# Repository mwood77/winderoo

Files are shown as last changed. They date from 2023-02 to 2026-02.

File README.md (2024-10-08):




<div align="center">  
  <h2>
    Winderoo
    <p><i>Open source firmware for microcontolled watch winders</i></p>
  </h2>
</div>

<div align="center"> 
  <a href="https://www.youtube.com/watch?v=BJKpY6Zp8BI" target="_blank">
    Winderoo - The Open Source Watch Winder
  </a>
  <br>
  <br>
  <p>
    Winderoo is open source firmware which adds <i>smart functionality</i> to your <a href="https://github.com/mwood77/osww" target="_blank">OSWW build</a> or microcontroller equipped watch winder. <i>Smart functionality</i> includes a Web UI (fully-translated in 5 languages!), OLED screen support, start timer, and more!
  </p>
</div>

> [!NOTE]
> OSWW is an open source modular watch winder, which you can read more about on [GitHub](https://github.com/mwood77/osww) or [Printables](https://www.printables.com/model/421249-osww-the-open-source-watch-winder).

### Key Features
* Settable RPD (rotations per day) between 100 - 960rpd
* Single direction (clockwise / anti-clockwise) or bi-directional winding.
* Settable start time. Have it wind while you're asleep, or while you're away, or anytime for that matter. 
* Manual cycle start / stop.
* 3 seconds of rest after 3 minutes of rotation, in every mode.
* Estimated cycle duration (how long it'll take to wind your watch).
* Cycle progress display (how far along the current winding routine is).
* Software or optional physical button to trigger ON/OFF state, so you can disable the winder completely.
* OLED screen support
* Simple setup. Flash the firmware and File System with a few clicks, then connect your phone (or other device) to the winder's setup wifi network & add it to your home network.
* There's no app required! You control it from a web browser.
* Minimal electronics / programming experience required
* Web UI is fully translated into 5 languages (more are welcome!)

### Winderoo Requires a Different Microcontroller
* **You must replace the Pi Pico, as spec'd in the OSWW build guide, with an ESP32. This project will not run on a Pi Pico!**

# User Manual
* [Click Here to see the user manual](./docs/user-manual.md)

## Prerequisites
> [!IMPORTANT]
> This project is an add-on to your already built [Open Source Watch Winder (OSWW)](https://github.com/mwood77/osww)

#### Download and install the following on your computer:
1. [Visual Studio Code](https://code.visualstudio.com/)
1. [PlatformIO](https://platformio.org/install/ide?install=vscode)
    - Note: the "extensions" button has changed since Platformio has created their install guide. You can access the extensions pane with the following key combinations:
        - Windows: Ctrl+Shift+X
        - macOS: Command+Shift+X
1. You may or may not need these drivers, but some 'knock off' ESP32 dev boards require them.
    - [CP210x Drivers](https://www.silabs.com/developers/usb-to-uart-bridge-vcp-drivers?tab=downloads) 
    - If the CP210x drivers don't work:  [CH340 Drivers](https://learn.sparkfun.com/tutorials/how-to-install-ch340-drivers) 

## Build Instructions
1. [Bill of Materials (what you need to buy)](./docs/bom-requirements.md)
1. [Software Installation](./docs/install-software.md)
1. [Winderoo Wiring Diagram](./docs/wiring-diagram.md)

## Contributing
This project welcomes contributions. Please follow the regular git workflow; fork + PR to contribute.

### Translations / Localization
Winderoo has multi-language support, and we welcome adding more languages.

To add another language:
1. Duplicate one of the current localizations, and translate the text:
    - `src/angular/osww-frontend/src/assets/i18n/` stores the current localizations.
1. Add a new language menu item here to enable your language:
    - `src/angular/osww-frontend/src/app/header/header.component.html`
1. Open a Pull Request

### Frontend
- Angular with Angular Material
- [Frontend Readme](./src/angular/osww-frontend/README.md)

### Backend 
- C++ based API with mDns, a web server, local file system, and a bunch of other things.

### API Specification

The API has 4 endpoints. You can explore them in the attached Open API definition.
- [Open API Definition](./openapi.yml)

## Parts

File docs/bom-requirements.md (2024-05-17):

> [👈 Back to main page](../README.md)

# Bill of Materials & Cost

> [!IMPORTANT]
> This project is an add-on to your already built [Open Source Watch Winder (OSWW)](https://github.com/mwood77/osww). 

- This microcontroller replaces the Pi Pico used in the OSWW.
- The Raspberry Pi Pico is incompatible with this project and must be swapped out.

### Total cost of required Parts
- **$8.00 (April 2023)**

> [!NOTE]
> The following tables contains affiliate links to Aliexpress; you do not pay an inflated price because of this. Should you decide to use another supplier, please ensure that you cross-reference this table and buy identical components.
>
> While most of these components are standardized, I will not be able to assist you if you purchase your components from a separate supplier, as the winder was designed around the components (as supplied) beneath.

| |  Quantity per Order | Link / Part Name |  Comments |  Cost Incl. Shipping |
| :-: | :---: | :---: | :---: |:-----:|
| 🔲 | 1 | [ESP32 Dev Kit](https://s.click.aliexpress.com/e/_Derbd5r) | Select `Color: ESP32` | $8.00 |

### Optional parts
The following parts list will allow you to add:
- 1x SSD1306 compatible OLED screen (0.96" size)
- 1x MX1508 Motor Controller. This is a much smaller DC motor controller. Winderoo supports granular motor control with this board (PWM control); you must set a build flag to use this, which has a callout step during the [software installation instructions](./install-software.md).

| |  Quantity per Order | Link / Part Name |  Comments |  Cost Incl. Shipping |
| :-: | :---: | :---: | :---: |:-----:
| 🔲  | 1 | [0.96" SSD1306 OLED](https://s.click.aliexpress.com/e/_DFywAW1) | Select: whichever colour you'd like! | $2.00 |
| 🔲  | 1 | [MX1508 Miniature Motor Controller (PWM)](https://www.aliexpress.com/item/4000408025093.html) |  | $3.00 |

## Next Steps
> [Proceed to software installation 👉](./install-software.md)

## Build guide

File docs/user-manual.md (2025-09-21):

> [👈 Back to main page](../README.md)

# User Manual

#### Contents
- [Winderoo's Web User Interface](#winderoos-web-user-interface)
- [Winderoo's Home Assistant Interface](#winderoos-home-assistant-interface)
- [Winderoo's LED Blink Status](#winderoos-led-blink-status)

## Winderoo's Web User Interface

| v1.1.0 | |
| :---: |:---: |
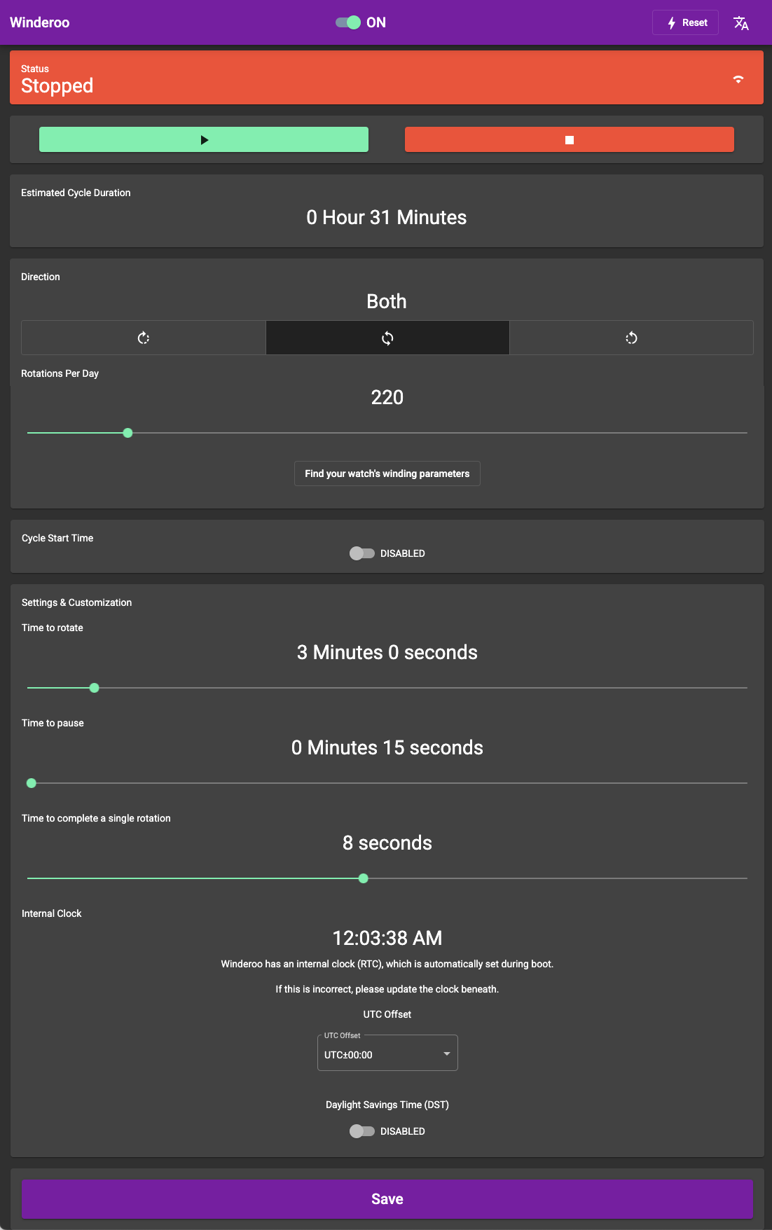
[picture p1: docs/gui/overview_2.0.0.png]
|  | This is winderoo's primary interface. From here you can change any settings you need |

### Enable / Disable Winding
| UI Element | Function |
| :---: |:---: |
|  | This is a software switch, which will _completely enable or disable_ the winder's ability to wind. When the switch is set to **OFF**, Winderoo will not wind or begin winding at a your desired 'Cycle Start Time.' If you choose to attach an (optional) physical button, the code will automatically toggle this switch when you press the button. |

### Reset / Change WiFi Network
| UI Element | Function |
| :---: |:---: |
|  | This is will open a pop-up window, which will ask you to confirm reset, and walk you through the reset procedure. Use this to change the WiFi network Winderoo connects to. |
|  | This will open a pop-up menu where you can select which language you'd prefer. |

### Status Bar
| UI Element | Function |
| :---: |:---: |
|  | Winder is not winding |
|  | Winder is winding |
| | Wifi Status - this behaves as you'd expect |

### Control Buttons
| UI Element | Function |
| :---: |:---: |
|  | _begin_ winding immediately, using saved settings |
|  | _stop_ winding immediately |

### Progress Indicator
> The progress indicator only appears while actively winding

| UI Element | Function |
| :---: |:---: |
|  | While animated, Winderoo is attempting to update the progress indicator |
|  | The progress of the current winding routine |

### Estimated Cycle Duration
| UI Element | Function |
| :---: |:---: |
|  | An estimation of how long the your current winding routine will take, start to finish |

### Winder Control
| UI Element | Function |
| :---: |:---: |
|  | Which direction Winderoo should turn. The available options are 'Clockwise,' 'Both' (clockwise + counter-clockwise), and 'Counter-Clockwise' |
|  | How many full rotations Winderoo should complete per routine |
|  | Launches a new browser tab to an external, 3rd party website. This resource hosts winding parameters for most major watch manufacturers |

### Cycle Start Time
| UI Element | Function |
| :---: |:---: |
|  | This will enable or disable the winder's timer. When the switch is set to **ENABLED**, Winderoo will begin winding at a your desired 'Cycle Start Time.' If the switch is set to **DISABLED**, you must start the winder using the [control buttons](#control-buttons) |
|  | Set which time you'd like Winderoo to begin winding at. **_Important!_** Winderoo will _always_ start at this time, even if you've already triggered a manual run with a [control button](#control-buttons). To stop this behavior, see: [Enable / Disable Winding](#enable--disable-winding) |

### OLED Screen

>[!IMPORTANT]
> This element will appear _only if_ you've compiled Winderoo with an OLED screen attached, and set the build flag accordingly.

| UI Element | Function |
| :---: |:---: |
|  | This will toggle the attached OLED screen on and off. |

### Screen Scheduling

> This functionality is only available when OLED screen is enabled.

| UI Element | Function |
| :---: |:---: |
|  | Enable or disable automatic screen scheduling. When enabled, the screen will automatically turn on and off based on the configured time schedule. |
|  | Set the time when the screen should turn on (24-hour format). |
|  | Set the time when the screen should turn off (24-hour format). |

**Note:** Screen scheduling works independently of manual screen control. When scheduling is enabled, the screen will automatically turn on/off based on the schedule, but you can still manually control the screen through the OLED toggle or Home Assistant integration.

### Settings & Customization

| UI Element | Function |
| :---: |:---: |
| | This sets the amount of time to rotate between pauses. Default is `3 minutes` |
| | This sets the amount of time to pause between rotation cycles. Default is `15 seconds` |
|  | This sets the amount of time it takes the winder to complete one full rotation. This value should only be changed if you've used a different motor, different gearing, or have retrofitted Winderoo into a off-the-shelf winder |
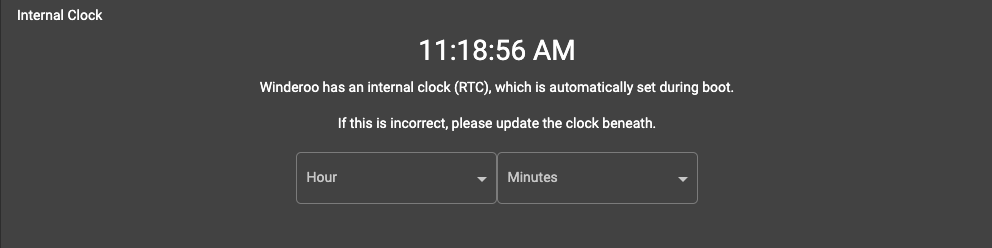
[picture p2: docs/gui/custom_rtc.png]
| | This reflects Winderoo's real time clock (RTC). This is set automatically using an NTP Pool. By default Winderoo's UTC offset is set to `0`. For accurate timekeeping, you must set this offset to your current location. You can use a site like [timeanddate.com](https://www.timeanddate.com/time/zone/timezone/utc) to search for your city and find your UTC offset. |

### Save / Update Settings
| UI Element | Function |
| :---: |:---: |
|  | This will capture and save all settings (including customizations). If a winding routine is currently running, it does not reset the current routine (it will update and finish accordingly). If you wish to make sure the routine is changed, manually stop, then start the routine. See [control buttons](#control-buttons). |

## Winderoo's Home Assistant Interface

>[!IMPORTANT]
> Home Assistant entities will only appear you've compiled Winderoo with the `HOME_ASSISTANT_ENABLED` build flag set to `TRUE`. If you're unsure how to do this, see the "**Build Options**" step under "*Flashing your microcontroller*" heading on the [Install Software](./install-software.md) documentation page.

If you've enabled Winderoo's Home Assistant integration, Winderoo will stream a number of entities into Home Assistant over MQTT. If you're unsure what MQTT or need to set this up in Home Assistant, [please see this document](https://www.home-assistant.io/integrations/mqtt).

Winderoo should be automatically discovered by Home Assistant within 60 seconds. The following entities are available to Home Assistant:
```yml
 -  button.winderoo_start
 -  button.winderoo_stop

 -  sensor.winderoo_status                                    : "Winding | Stopped"
 -  sensor.winderoo_wifi_reception                            : "Excellent | Good | Fair | Poor"
 -  sensor.winderoo_rtc_epoch_time                            : <unix epoch>
 
 -  number.winderoo_rotations_per_day                         : 100 <-> 960 
 -  number.winderoo_time_to_rotate                            : 100 <-> 960 
 -  number.winderoo_time_to_pause                             : 10 <-> 900 
 -  number.winderoo_duration_to_complete_a_single_rotation    : 1 <-> 16 

 -  select.winderoo_direction                                 : "CCW | BOTH | CW"
 -  select.winderoo_hour                                      : 00 <-> 23
 -  select.winderoo_minutes                                   : 00 <-> 50
 -  select.winderoo_rtc_hour                                  : 00 <-> 23
 -  select.winderoo_rtc_minutes                               : 00 <-> 59
 
 -  switch.winderoo_timer_enabled                             : "true | false"
 -  switch.winderoo_oled                                      : "true | false"
 -  switch.winderoo_power                                     : "true | false"
 -  switch.winderoo_screen_schedule_enabled                   : "true | false"
 -  select.winderoo_screen_schedule_start_hour                : 00 <-> 23
 -  select.winderoo_screen_schedule_start_minute              : 00 <-> 50
 -  select.winderoo_screen_schedule_end_hour                  : 00 <-> 23
 -  select.winderoo_screen_schedule_end_minute                : 00 <-> 50
```

You can replicate Winderoo's GUI with a basic Home Assistant card:
<table align="center">
  <tr>
    <th>Home Assistant GUI</th>
    <th>Code</th>
  </tr>
  <tr>
    <td>
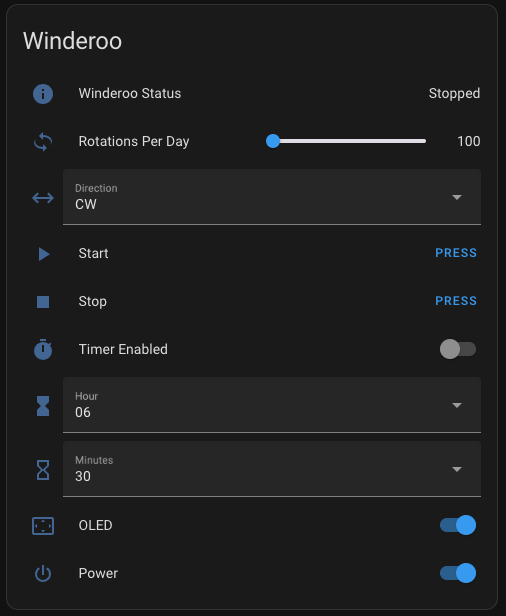
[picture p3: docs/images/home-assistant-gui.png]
        
    </td>
    <td>
<pre><code>
type: entities
entities:
- entity: sensor.winderoo_status
- entity: number.winderoo_rotations_per_day
    name: Rotations Per Day
- entity: select.winderoo_direction
    name: Direction
- entity: button.winderoo_start
    name: Start
- entity: button.winderoo_stop
    name: Stop
- entity: switch.winderoo_timer_enabled
    name: Timer Enabled
- entity: select.winderoo_hour
    name: Hour
- entity: select.winderoo_minutes
    name: Minutes
- entity: switch.winderoo_oled
    name: OLED
- entity: switch.winderoo_power
    name: Power
title: Winderoo
show_header_toggle: false
</pre></code>
    </td>
  </tr>
  <tr>
    <td>
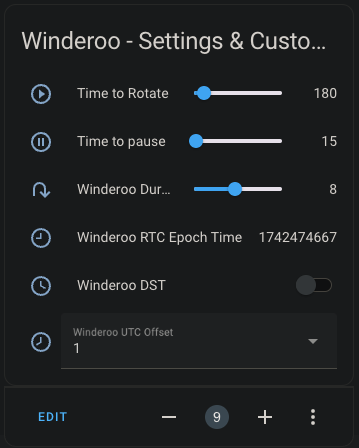
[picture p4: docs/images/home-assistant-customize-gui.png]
        
    </td>
    <td>
<pre><code>
type: entities
entities:
  - entity: number.winderoo_time_to_rotate
    name: Time to Rotate
  - entity: number.winderoo_time_to_pause
    name: Time to pause
  - entity: number.winderoo_duration_to_complete_a_single_rotation
  - entity: sensor.winderoo_rtc_epoch_time
  - entity: switch.winderoo_dst
  - entity: select.winderoo_utc_offset
title: Winderoo - Settings & Customization
</pre></code>
    </td>
  </tr>
</table>

## Winderoo's LED Blink Status

- Most ESP32 dev boards have a primary RED LED that is always on. This cannot be shut off via firmware. 
    - If you find it bothersome, you can cover it with electrical tape, de-solder it, or cut the trace with an x-acto knife.

- Most ESP32 dev boards have a secondary BLUE LED, however some may be a different colour. 
    - Please use the following table to understand what Winderoo is telling you.

| ESP32 Board (or optional external LED) | LED State | Meaning |
| :---: | :---: | :---: |
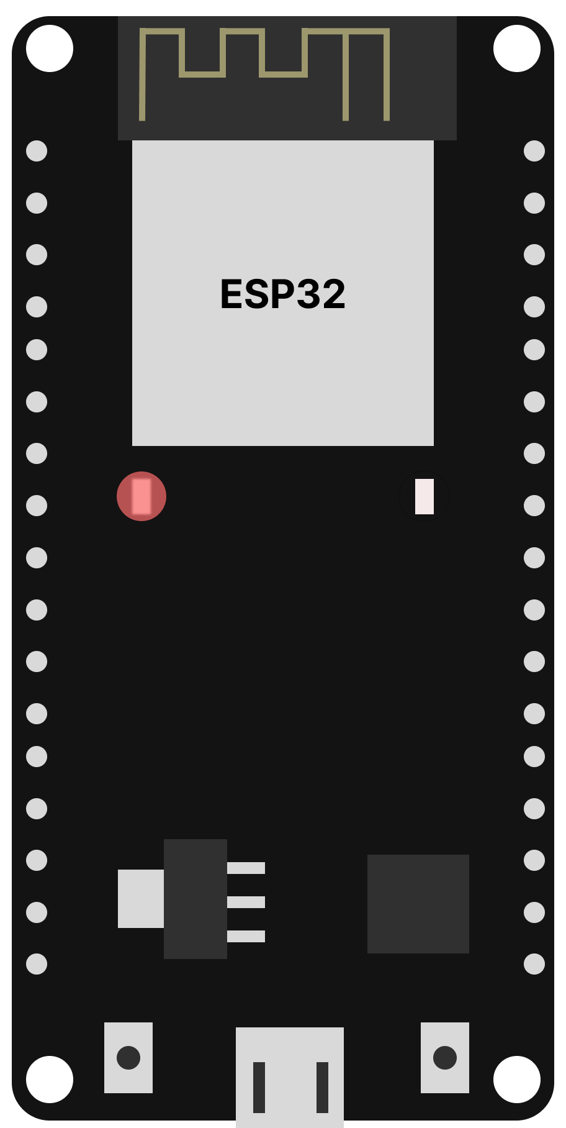
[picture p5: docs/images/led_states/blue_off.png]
|   | secondary LED is not illuminated | Winderoo is operational. |
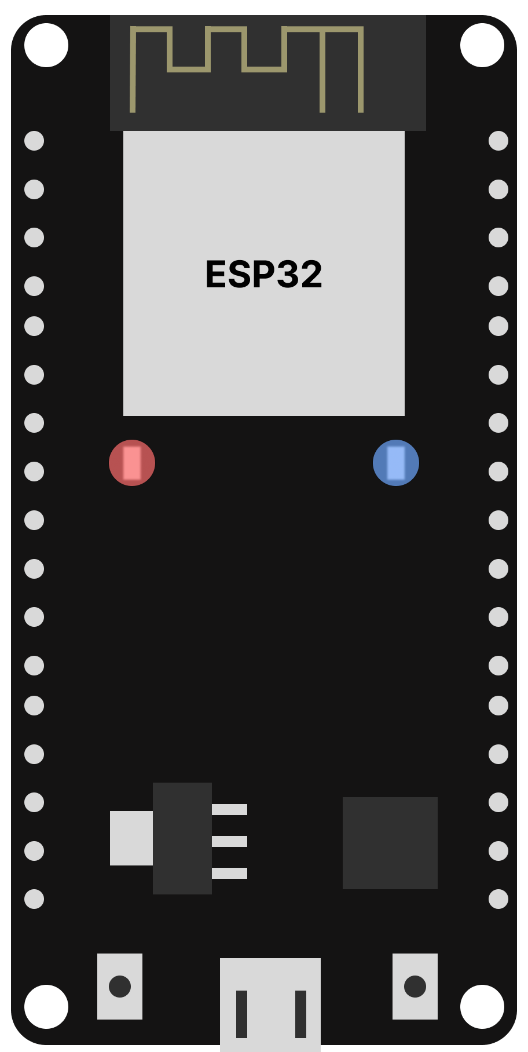
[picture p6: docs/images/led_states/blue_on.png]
|   | secondary LED is illuminated  | Winderoo is ready for setup. Connect to the WiFi network called "Winderoo Setup" and add Winderoo to your WiFi network. |
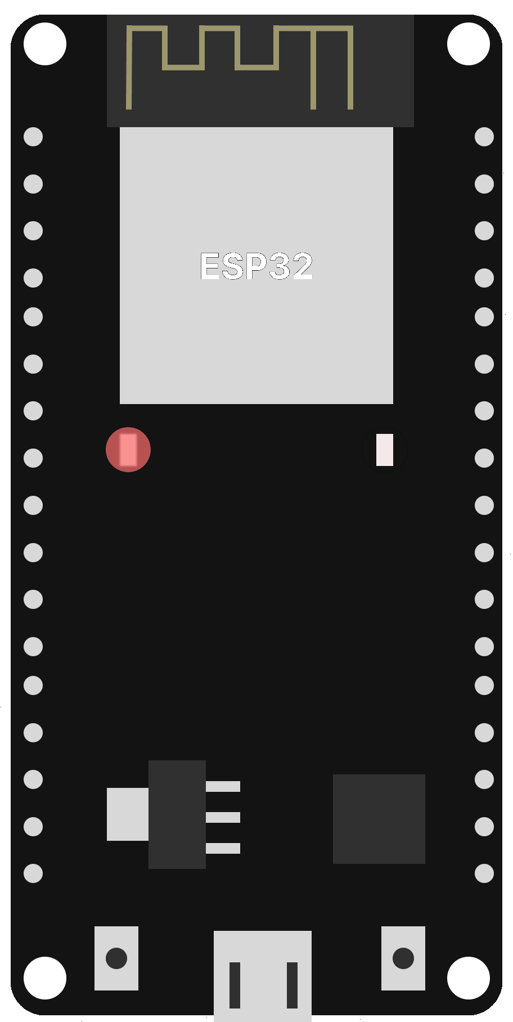
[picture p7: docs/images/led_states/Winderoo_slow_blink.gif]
|  | slow blinking | Winderoo has successfully connected to your WiFi network. When the the **BLUE LED** stops blinking, you may access Winderoo's UI from your web browser. |
|  | fast blinking | Winderoo is resetting, wait until the **BLUE LED** turns solid to begin WiFi setup. |
|   | extremely slow blinking | Winderoo's winding capabilities have been turned 'OFF' via the software switch, or an optional physical button. Winderoo will not wind until it has been turned to 'ON.' |

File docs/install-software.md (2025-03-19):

> [👈 Back to main page](../README.md)

# Software Installtion & Flashing your ESP32

> [!IMPORTANT]
> This project is an add-on to your already built [Open Source Watch Winder (OSWW)](https://github.com/mwood77/osww).

- This project requires a microncontroller which replaces the Pi Pico used in the OSWW.
- The Raspberry Pi Pico is incompatible with this project and must be swapped.

# Getting Started

### Prerequisites
- Download [Visual Studio Code (VSCode)](https://code.visualstudio.com/download)
- Download [PlatformIO](https://platformio.org/install/ide?install=vscode)

## Flashing your microcontroller

1. Download this repository. You can do this via git or by downloading the repository as a ZIP.
    - If you downloaded the repository as a zip, uzip it before proceeding to step 2.
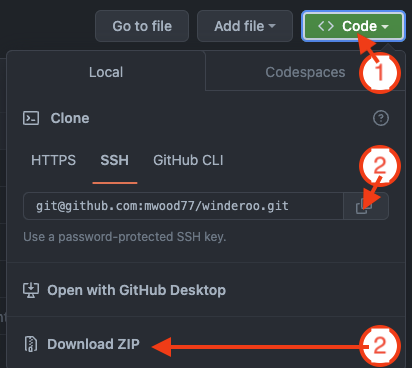
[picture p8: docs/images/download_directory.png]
how to download
    
1. Open the extracted folder (or cloned repository if using git) in Visual Studio Code
1. **Build Options - (PWM, OLED, Home Assistant)**
    -  if you're building Winderoo with an OLED screen, intend to use Home Assistant, or you desire fine-grained motor control (pulse width modulation), you must enable some of the following build flags to tell PlatformIO to include additional libraries.
    - To toggle these build flags, navigate to the file called `platformio.ini`:
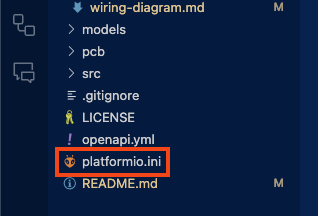
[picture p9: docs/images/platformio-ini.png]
            
        - In this file, you'll see the following block of code:
            ```yml
            build_flags =
                -D OLED_ENABLED=false
                -D PWM_MOTOR_CONTROL=false
                -D HOME_ASSISTANT_ENABLED=false
            ```
            - Change `-D HOME_ASSISTANT_ENABLED=false` to `-D HOME_ASSISTANT_ENABLED=true` to enable Winderoo's Home Assistant integration
                - > 🚦 I'd strongly recommend you have a dedicated MQTT user; do not use your main account.

                - If this feature is enabled, you must add your Home Assistant's IP, username, and password.
                    - You can add them in [`main.cpp`](https://github.com/mwood77/winderoo/blob/main/src/platformio/osww-server/src/main.cpp#L51-L54) inside the configuration block:
                    ```cpp
                    // Home Assistant Configuration
                    const char* HOME_ASSISTANT_BROKER_IP = "YOUR_HOME_ASSISTANT_IP";
                    const char* HOME_ASSISTANT_USERNAME = "REPLACE_THIS_WITH_HOME_ASSISTANT_LOGIN_USERNAME";
                    const char* HOME_ASSISTANT_PASSWORD = "REPLACE_THIS_WITH_HOME_ASSISTANT_LOGIN_PASSWORD";
                    ```
            - Change `-D OLED_ENABLED=false` to `-D OLED_ENABLED=true` to enable OLED screen support
            - Change `-D PWM_MOTOR_CONTROL=false` to `-D PWM_MOTOR_CONTROL=true` to enable PWM motor control; at the time of writing, Winderoo with PWM only supports `MX1508` derived motor controllers.
                - > `PWM_MOTOR_CONTROL` is an experimental flag. You will encounter incorrect cycle time estimation and other possible bugs unless you align the motor speed to **20 RPM** (see [Troubleshooting](#troubleshooting)). Use at your own risk.
    - PlatformIO will now compile Winderoo with OLED screen, Home Assistant, and or PWM motor support
1. Select 'PlatformIO' (alien/insect looking button) on the workspace menu and wait for visual studio code to finish initializing the project
    <div align="center">platformIO button</div>
1. Expand the main heading: **"esp32doit-devkit-v1"**:
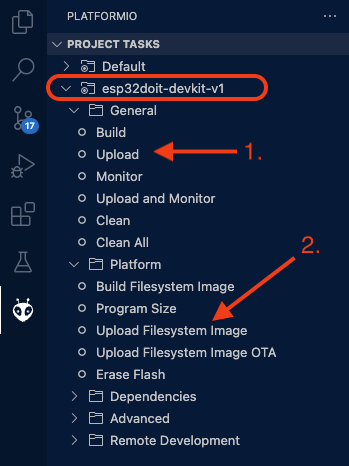
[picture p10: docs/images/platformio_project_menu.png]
platformIO actions overview
    
1. Expand the "General" heading, then click **Upload**. You'll see a message if the code was uploaded successfully:
    <div align="center">code upload button</div>

    > [!IMPORTANT]
    > This step is separate than the step beneath.
    > 
    > You must do both steps; **Upload** and **Upload Filesystem Image**.
1. Now expand the "Platform" heading, then click **Upload Filesystem Image**. You'll see a message if the code was uploaded successfully:
    <div align="center">upload filesystem button</div>
1. All done! Your microcontroller should now have 2 LEDs illuminated (see beneath). If it does, proceed to [Next steps](#next-steps). If not, try to upload the code & file system again.
    <div align="center">upload filesystem button</div>
1. If you have a different LED state, compare it with this table:
    - [Understanding Winderoo's LED Blink Status](user-manual.md#understanding-winderoos-led-blink-status)

## Next steps

Ok, you've got 2 LEDs illuminated on your board. Great! Let's make sure the code works.

1. Get out your mobile device (phone/tablet) and navigate to the Wi-Fi / wireless network list. You'll want to find and join a WiFi network called "**Winderoo Setup**."
    - It may take a minute or so to connect, or look like it isn't doing anything. Hold tight, it is.
1. Once you've connected to "**Winderoo Setup**", a captive page will open called "WifiManger Winderoo Setup."
1. Tap "Configure WiFi"
1. Tap on the network you want to add Winderoo to, this is likely your home WiFi network
1. Enter your WiFi network's password then tap "Save." Wait until the captive page closes itself.
1. Re-join your home WiFi network
1. Open up a web browser and try to navigate to the following webpage:
    - [http://winderoo.local/](http://winderoo.local/)
1. If you see Winderoo's user interface, you're all done!
    - [Here is an overview of Winderoo's user interface](./user-manual.md)

## Troubleshooting
### Motor Turns too fast when using PWM
> [!WARNING]
> PWM_MOTOR_CONTROL is an experimental flag. You will encounter incorrect cycle time estimation and other possible bugs unless you align the motor speed to **20 RPM**.

- The default speed is `145` (8-bit resolution), where `0` is the slowest and `255` is the fastest. You can modify this value here:
    - [`MotorControl.cpp`](../src/platformio/osww-server/src/utils/MotorControl.cpp#L7)
        - Change the value for the variable `motorSpeed` to any value between `0` and `255`
        - After changing that value, you must recompile the software and upload it to your ESP32
- You can also tweak the rotational timing value. By default this is set at 8 seconds to complete one revolution.
    - To change this value, change the variable `durationInSecondsToCompleteOneRevolution` here:
    -  [`main.cpp`](../src/platformio/osww-server/src/main.cpp#L38)

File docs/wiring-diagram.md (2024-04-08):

> [👈 Back to main page](../README.md)

# Wiring Diagrams - Winderoo
- [Winderoo](#winderoo)
- [Winderoo With OLED Screen](#winderoo-with-oled-screen)

## Winderoo
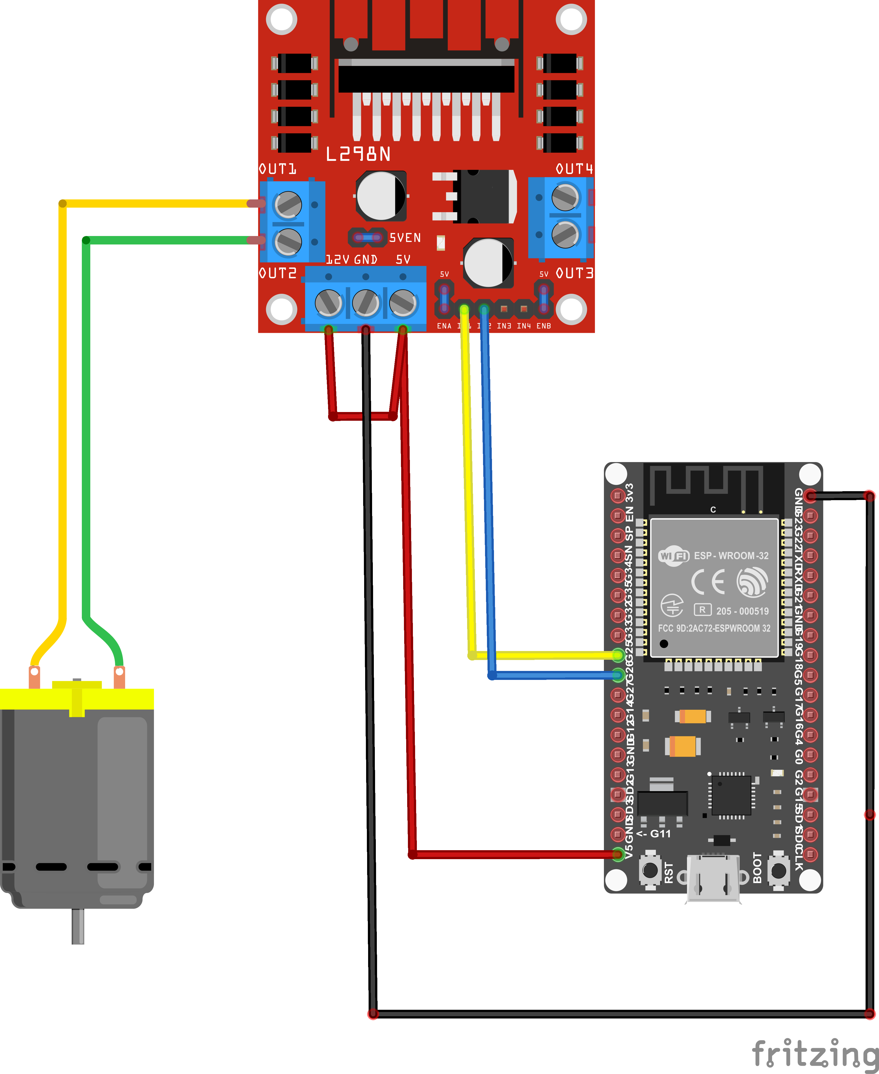
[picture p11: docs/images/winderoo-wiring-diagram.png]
fritzing wiring diagram


<div align="center">
    <a href="./winderoo-wiring-diagram-fritzing.pdf">Is the image hard to view? Open the PDF instead</a>
</div>
<br />

- Connect the ESP32's `5V` Output pin to the 5V input of the L298N driver board (red wire)
- Connect a ground from the ESP32 to the L298N driver board (black wire)
- Connect the L298N driver board's 5V and 12V terminals together (red jumper wire)
- Make sure the L298N's jumpers are in place (small blue wires on board)
- Connect the ESP32's `GPIO25` to `IN1` on the L298N driver board (yellow wire)
- Connect the ESP32's `GPIO26` to `IN2` on the L298N driver board (blue wire)
- Connect the DC motor to channel 1 on the L298N driver board.
    - > Note: polarity does not matter here
    - You may add an external button off `GPIO 13` on the ESP32; this will enable and disable winding

## Winderoo with OLED Screen

> [!IMPORTANT]
> This wiring diagram assumes you've purchased an I2C 4-wire OLED (SSD1306 driver compatible). Complex LCDs are currently not supported.

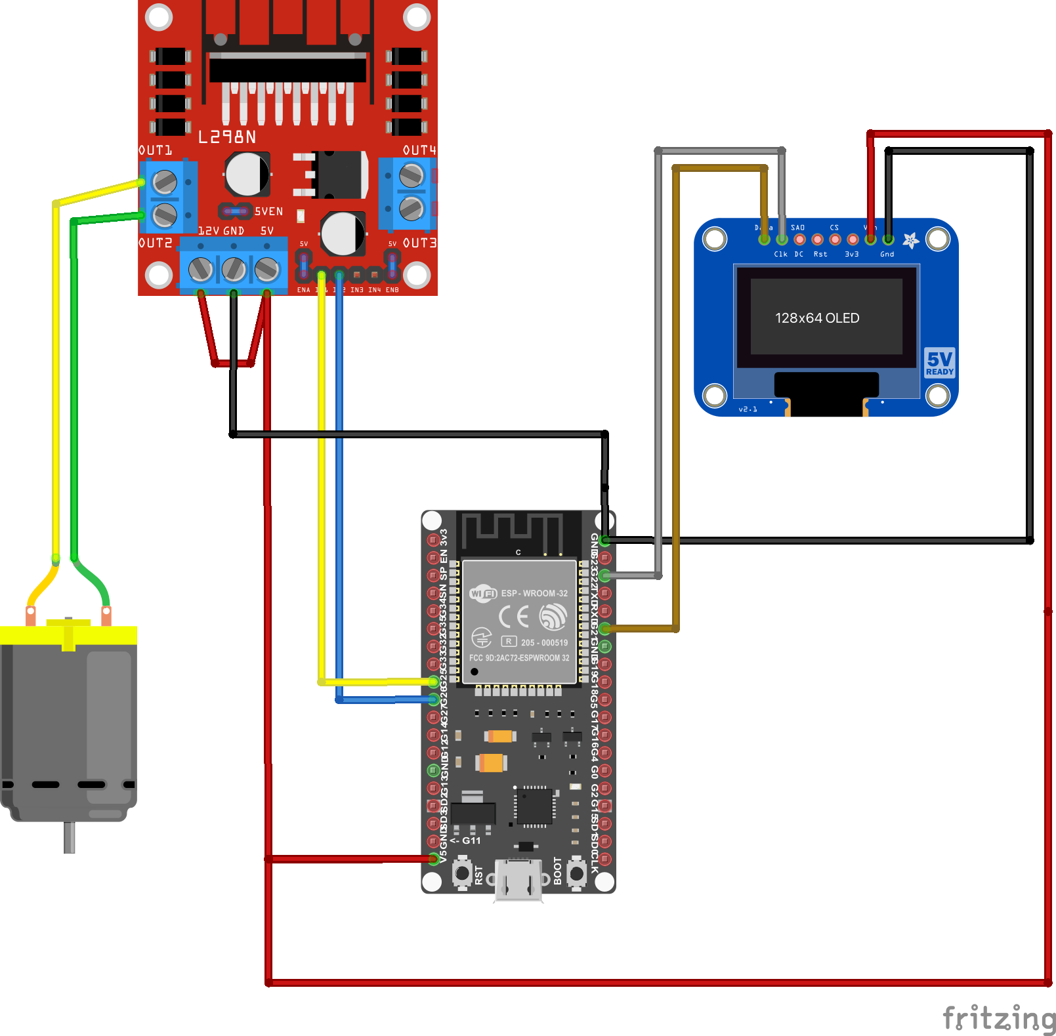
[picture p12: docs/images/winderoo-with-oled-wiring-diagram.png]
fritzing wiring diagram


<div align="center">
    <a href="./winderoo-with-oled-wiring-diagram.pdf">Is the image hard to view? Open the PDF instead</a>
</div>
<br />

- Connect the ESP32's `5V` output pin to the 5V input of the L298N driver board (red wire)
- Connect the ESP32's `5V` output pin to the `VCC` input pin on your OLED screen
- Connect a ground wire from the ESP32 to the L298N driver board (black wire)
- Connect a ground wire from the ESP32 to the OLED screen's `GRND` pin
- Connect a wire from the ESP32's `D22` pin to the OLED screen's `SCL` pin
- Connect a wire from the ESP32's `D21` pin to the OLED screen's `SDA` pin
- Connect the L298N driver board's 5V and 12V terminals together (red jumper wire)
- Make sure the L298N's jumpers are in place (small blue wires on board)
- Connect the ESP32's `GPIO25` to `IN1` on the L298N driver board (yellow wire)
- Connect the ESP32's `GPIO26` to `IN2` on the L298N driver board (blue wire)
- Connect the DC motor to channel 1 on the L298N driver board.
    - > Note: polarity does not matter here
    - You may add an external button off `GPIO 13` on the ESP32; this will enable and disable winding

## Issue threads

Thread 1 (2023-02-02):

Investigate WiFi Manager callbacks for webserver / mDNS autostart after captive portal success

mwood77, 2023-02-02:
Winderoo must be physically reset after successfully connecting to a user's WiFi network; this is inconvenient.

Investigate whether a callback exists that can trigger the webserver & mDNS to start after successfully changing wifi networks.

mwood77, 2023-02-05:
b583128

```
...
wm.setSaveConfigCallback(saveWifiCallback);

void saveWifiCallback() {
  // Slow blink to confirm success & restart
  for ( int i = 0; i < 6; i++ ) {
    digitalWrite(LED_BUILTIN, HIGH);
    delay(500);
    digitalWrite(LED_BUILTIN, LOW);
    delay(500);
  }
  ESP.restart();
}
```

Closed 2023-02-05.

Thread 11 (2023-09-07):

mDNS stops working after ~2 minutes

Anumann, 2023-09-07:
I'm basically seeing this issue - any idea if there's an easy fix?

https://github.com/espressif/arduino-esp32/issues/4406

mwood77, 2023-09-15:
I had a quick look at this, but I'm unable to debug it as I'm away from my dev station for a week or so.

The base library `ESPmDNS` used in Winderoo has a comment about calling an `update()` method in the primary loop (it would be called as `MDNS.update()` at line 600 in Winderoo's `main.cpp`). However, I don't see this method existing in the library.

Are you using a Windows PC to when you try to resolve `winderoo.local`?

Anumann, 2023-09-15:
Yeah, I'm using a Windows PC. I can also test with an Android phone, if that would be helpful to test or rule anything out.

mwood77, 2023-09-16:
give it a shot with your android phone too - I remember there may have been an issue with them. I can look at it again when I'm back in the country.

Anumann, 2023-09-21:
@mwood77 sorry for the delayed response. I did some more testing - I cannot resolve the webpage winderoo.local on either my Android (using the local wifi) or my Windows PC.

One more test which also suggests to me DNS isn't working as expected - I started a ping in Windows right when the system powered on (in windows cmd window, I ran "ping winderoo.local -t"). Since the DNS resolution was working initially, the pings continued successfully even when the webpage started to fail to load.

mwood77, 2023-10-10:
Interesting - I'll look at it this week and get back to you

Closed 2023-11-02.

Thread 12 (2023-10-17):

Bill of materials list links aren't working anymore

JRM-PT, 2023-10-17:
Hi, I tried to follow the link for the ESP32 board but it no longer exists. Unfortunately there's a ton of slightly different ESP32 boards at AliExpress and the more inexperienced of us (me on top of that list) are afraid to get a wrong one

mwood77, 2023-10-17:
Hi @JRM-PT , thanks for letting me now.

I'll try to setup a chron job to check my repositories and alerts me to broken links. This has happened a couple times.

Almost any ESP32 should work on this project, like these:
- https://www.aliexpress.com/item/1005002611857804.html (If you're worried, select the `Color: ESP32` and not the other ones)

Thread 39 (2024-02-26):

Issue with mDNS and Android

eengnr, 2024-02-26:
It seems that mDNS doesn't work properly on Android which causes the Winderoo web UI to not work anymore after #36. At least I couldn't get it to work... 😅

It turned out that I cannot resolve `http://winderoo.local` on any Android device (7, 12, 13, 14).
Before the change in #36, it was possible to access the web UI with the IP of the ESP32 on Android and the API call was then done towards the IP. With my change in #35, the API call would be done to any domain that was used for the UI (which is of course accessible, otherwise the UI would not load at all).

But now since #36, the API call is always done to `http://winderoo.local`, even if the IP is used to load the UI or if a custom non-.local-domain name is used (I can set this with AdGuard Home in my LAN).

I did some research and found some issues where this one seems to be quite similar to my problem:
https://github.com/espressif/arduino-esp32/issues/9051

https://github.com/esphome/issues/issues/3003

I can access the `.local` domain which is broadcasted from a Raspberry Pi with OpenHAB, but I cannot access the `.local` from the ESP32 on Android.
On Linux or iOS it works fine.

Long story short - @mwood77 do you observe the same with an Android device? Or does it work for you on Android? I'm currently not sure if it's an issue in my network or an issue in the combination Android + mDNS on ESP32.

To not be dependent on mDNS, perhaps the web UI could load the API from the IP of the ESP32 instead of the mDNS `.local` domain?

mwood77, 2024-02-26:
Couple more follow-up questions.

Do you see anything from your android devices with the following urls:

- `http://winderoo.local/` - make sure the trailing slash is in the address)
- `http://winderoo.local/api/status` - if you have a device on the network, this will provide you with the device's current state.

Reading through Google's Android issue tracker, it looks like multicast dns was implemented in Android 12 and rolled out to Pixel devices. However, I can't say how that roll-out is handled by other manufacturers.

See here:
- https://issuetracker.google.com/issues/140786115?pli=1

eengnr, 2024-02-27:
Thanks for the detailed feedback! I hope this answers your questions :)

Q: What android device are you using?
A: Pixel 7 with stock Android 14. But issue also happens e.g. on a Pixel 3 XL with stock Android 12.

Q: You can normally access .local domains without issue?
A: This was never a use case for me, because all devices have a static IP in my network and I assign internal `.home` domains with AdGuard Home as DNS. But it turned out that OpenHAB advertises itself with a `.local` domain as well and I can access it from Android without a problem. The problem only exists for the ESP.

Q: Do you have any devices running esphome, or home assistant on your network, that you can access from your android device?
A: No other ESP32 or Home Assistant. I'm using OpenHAB, see above :)

Q: I assume you're also seeing no abnormal logs coming over serial for the web server?
A: Yes, looks ok:
```
[STATUS] - connected to saved network
[STATUS] - mDNS started
```

Q: Do you see anything from your android devices with the following urls
A: No, I get DNS_PROBE_FINISHED_NXDOMAIN in Chrome and "Adress not found" in Firefox

Some additional comments:

> Reading through Google's Android issue tracker, it looks like multicast dns was implemented in Android 12 and rolled out to Pixel devices

It seems to be part of the Play Services -> https://www.androidpolice.com/android-mdns-local-hostname/
Therefore it should be available on older Android versions, too.

> Glancing at the old front-end logic, the url sanitization only happened when the FE was accessed during local development...

Rolling back to commit `8058d30`, the FE does the API call towards the IP if I load the FE from the IP `http://192.168.0.120` (in my case) instead of `http://winderoo.local`. I just flashed that commit to the ESP, no local FE development involved. With that, it's possible to use it from Android by accessing the FE with the IP of the ESP.
This has changed, since commit `6592d1b` the FE always does the API call towards `http://winderoo.local` which breaks the FE on my Android devices completely.
For local development of the FE I think the API calls should go to `winderoo.local` if the `window.location.href` includes `localhost` or `127.0.0.1` and not `192`.

> Implementing this won't fix your issue though right, as you'll still have difficulty resolving the root domain (front end) http://winderoo.local.

That's right, but at least it would be possible to access a working FE from the IP of the ESP. Currently, the winderoo.local is hardcoded and if access is not possible, it breaks the FE even if the FE is loaded from the IP.

> I'll see if I can sink some more time into this tomorrow.

Please don't put too much effort in it :slightly_smiling_face:  It could still be an issue on my side - I just wanted to ask if it's reproducible for you (or perhaps someone else using Winderoo with Android).

I'll provide another PR which brings back the `window.location.href` check and respects the `localhost`/`127.0.0.1` for local FE development. This should at least allow to load the FE from the IP or any custom domain name in case mDNS is not working.

mwood77, 2024-03-07:
Seeing as #40 is merged, i'm going to close this for now. In the future, we need to work out a better solution for android users.

Closed 2024-03-07.

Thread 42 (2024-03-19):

Wifi setup not working

Lu-ni, 2024-03-19:
Hey!
Firstly, thanks a lot for the project, I'm currently building one.

I'm encountering a issues when I follow the step to setup the winderoo.

-  DONE : Connection to winderoo wifi
-  DONE : selecting my wifi and putting the password (tried on 3 different wifi)

After those step I'm stuck on the page "Saving Credentials \n Trying to connect ESP to network ...."

Do you have any clue on how I can debug that ?

Lucas

mwood77, 2024-03-20:
Hey Lucas!

This can take some time - if you leave it for 60 seconds or so after you see "Saving Credentials...." on your phone, does the second (blinking) LED on the Winderoo board turn off? If so, that means it has successfully connected.

Also, how far away from your access point is the Winderoo? These boards don't have amazing reach, but it's usually strong enough to span some distance (I can reach across 2 floors in my wooden-structured home).

Lu-ni, 2024-03-21:
Thank you for your fast answer, I'll try again tomorrow !

Closed 2024-04-01.

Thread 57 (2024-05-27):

After Upgrading to version 2.0 stops working - Blue led blinking

tuliosilvajunior, 2024-05-27:
After the upgrade process is successful, the connection to the wireless working is flapping, and the blue led is blinking variating the speed. It returns 1 ping and then a lot of timeouts.
If I erase the flash and downgrade to the version 1.0 everything works fine. Any Idea how to debug?
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

mwood77, 2024-05-28:
That's a new one.

When you're seeing these timeouts, the onboard LED is blinking? Can you connect it to your computer and see what is happening in the Serial Monitor?

Closed 2024-06-25.

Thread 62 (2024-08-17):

Add Home Assistant Integration

TomYoungs, 2024-08-17:
Hey!

This might already be possible but would be nice to be able to control it via a home assistant dashboard, see when it's running etc, would fit into peoples automations as well which would be cool

Thanks,
Tom

mwood77, 2024-08-19:
Interesting idea - what kind of features would you expect from that?

You could actually interact with winderoo via home assistant automations right now, if you use the [`RESTful Command` integration](https://www.home-assistant.io/integrations/rest_command/).

For example, I think this is all you'd need to get yourself up and running:

```yaml
rest_command:
  winderoo_change_timer:
    url: "http://winderoo.local/api/timer"
    method: POST
    payload: "timerEnabled={{ timerEnabled }}"
    content_type: "application/x-www-form-urlencoded"

  winderoo_change_state:
    url: "http://winderoo.local/api/update"
    method: POST
    content_type: "application/json"
    payload: >
      {
        "tpd": "{{ tpd }}",
        "hour": "{{ hour }}",
        "minutes": "{{ minutes }}",
        "timerEnabled": "{{ timerEnabled }}",
        "action": "{{ action }}",
        "rotationDirection": "{{ rotationDirection }}",
        "screenSleep": {{ screenSleep | lower }}
      }

  winderoo_toggle_power:
    url: "http://winderoo.local/api/power"
    method: POST
    content_type: "application/json"
    payload: '{"winderEnabled": "{{ winderEnabled }}"}'

  winderoo_reset:
    url: "http://winderoo.local/api/reset"
    method: GET

  winderoo_get_status:
    url: "http://winderoo.local/api/status"
    method: GET
    content_type: "application/json"
```

Then you'd call it in an automation like:

```yaml
# my automation

automation:
- alias: "Arrive at Work"
  trigger:
    platform: zone
    entity_id: device_tracker.my_device
    zone: zone.work
    event: enter
    action:
      - service: rest_command.winderoo_change_state
        data:
          tpd: "330"
          hour: "14"
          minutes: "30"
          timerEnabled: "1"
          action: "START"
          rotationDirection: "BOTH"
          screenSleep: false
    mode: single # you may or may not need this "mode: single" part
```

mwood77, 2024-10-07:
@TomYoungs proper home assistant integration is coming over MQTT. Most of the work required has been completed. Will likely release it in the next 48 hours.

see #66

mwood77, 2024-10-08:
✅  Home Assistant is available as of release 3.0.0 (main branch)

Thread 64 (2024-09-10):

Winder only runs CCW regardless of setting

markbyrne, 2024-09-10:
I have set CW, 800 with a start time of 10:00, but noticed it was running CCW. When I manually start and stop it also only runs CCW. It was working properly yesterday...

mwood77, 2024-09-12:
That's strange. Have you refreshed the page on `Winderoo.local` to make sure the GUI is up to date?

Also, you can query winderoo's state directly with:

[winderoo.local/api/status](winderoo.local/api/status)

I'm away from my winders right now, but the response should have a field called "direction" and the possible values that it could return are: `CW | BOTH | CCW`

burgosgts, 2025-01-31:
Good afternoon, first of all, thank you for the great work. I have the same problem, the motor only turns CW. Regardless of the mode I put it in, it recognizes the three modes but only turns clockwise.

markbyrne, 2025-02-17:
This issue had resolved, but I just got back from a tip and the issue re-emerged.

{"status":"Winding","rotationsPerDay":"800","direction":"CW","hour":"12","minutes":"00","durationInSecondsToCompleteOneRevolution":8,"startTimeEpoch":1738449903,"currentTimeEpoch":1738449933,"estimatedRoutineFinishEpoch":1738462603,"winderEnabled":"1","timerEnabled":"1","db":-69,"screenSleep":false,"screenEquipped":false}

It appears CW should be set, but it is spinning CCW.

mwood77, 2025-02-18:
Hi all do you know what version you've installed?

The front end and the back end are both versioned;

## Backend
- If you have an OLED screen attached, it'll flash the version on boot. If not, you can open up the source code and see what it is at this line:
https://github.com/mwood77/winderoo/blob/main/src/platformio/osww-server/src/main.cpp#L97

## Frontend
- Tap "Reset" and at the bottom of the pop-up, the version is listed there.

markbyrne, 2025-02-18:
Looks like 1.0.0

mwood77, 2025-02-19:
Could you please pull the code again (download the code in the `main` branch) and re-flash your microcontroller?

markbyrne, 2025-03-06:
I just re-flashed, reconnected it to wifi, set the settings, saved, hit run, and it ran in CW for ~5 seconds, then reversed and only runs in CCW again regardless of my settings.

markbyrne, 2025-03-07:
{"status":"Winding","rotationsPerDay":"800","direction":"CW","hour":"10","minutes":"00","durationInSecondsToCompleteOneRevolution":8,"startTimeEpoch":1740765449,"currentTimeEpoch":1740765462,"estimatedRoutineFinishEpoch":1740778149,"winderEnabled":"1","timerEnabled":"1","db":-66,"screenSleep":false,"screenEquipped":false}

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

It is winding CCW.

mwood77, 2025-03-19:
@markbyrne I've finally had some time to sit down with this.

I've completely wiped my test setup, re-built the frontend, and flashed the microcontroller with the code in `main`.

Versions:
- `main.cpp` is `String winderooVersion = "3.0.0";`
- Frontend is `1.1.0`

<hr />

### Direction is set to `BOTH`

API `/status` response:
```
{
    "status": "Winding",
    "rotationsPerDay": "220",
    "direction": "BOTH",
    "hour": "00",
    "minutes": "00",
    "startTimeEpoch": 1162,
    "currentTimeEpoch": 1812,
    "estimatedRoutineFinishEpoch": 3057,
    "winderEnabled": "1",
    "timerEnabled": "0",
    "db": -43,
    "screenSleep": false,
    "screenEquipped": true,
    "customWindDuration": "180",
    "customWindPauseDuration": "15",
    "customDurationInSecondsToCompleteOneRevolution": 8
}
```

✅  In this state, winding direction works correctly; alternates.

<hr />

### Direction is set is `CW`

API `/status` response:
```
{
    "status": "Winding",
    "rotationsPerDay": "220",
    "direction": "CW",
    "hour": "00",
    "minutes": "00",
    "startTimeEpoch": 1837,
    "currentTimeEpoch": 1981,
    "estimatedRoutineFinishEpoch": 3732,
    "winderEnabled": "1",
    "timerEnabled": "0",
    "db": -44,
    "screenSleep": false,
    "screenEquipped": true,
    "customWindDuration": "110",
    "customWindPauseDuration": "15",
    "customDurationInSecondsToCompleteOneRevolution": 8
}
```

✅  In this state, winding direction consistently starts & stops, and **only winds clockwise**

<hr />

### Direction is set is `CCW`

API `/status` response:
```
{
    "status": "Winding",
    "rotationsPerDay": "220",
    "direction": "CCW",
    "hour": "00",
    "minutes": "00",
    "startTimeEpoch": 2156,
    "currentTimeEpoch": 2165,
    "estimatedRoutineFinishEpoch": 4156,
    "winderEnabled": "1",
    "timerEnabled": "0",
    "db": -44,
    "screenSleep": false,
    "screenEquipped": true,
    "customWindDuration": "110",
    "customWindPauseDuration": "15",
    "customDurationInSecondsToCompleteOneRevolution": 8
}
```

✅ In this state, winding direction consistently starts & stops, and **only winds counter clockwise**

<hr />

Are you _certain_ everything is wired correctly on your unit?

mwood77, 2025-04-29:
Hey @yannicschuller  - thanks for letting me know. Can you dump your `platform.ini` file here please?

mwood77, 2025-04-29:
- Are you using the default motor controller (L298N) or a different motor controller?
- Is your BE version `4.0.0`? See this line: https://github.com/mwood77/winderoo/blob/216bb8400f6aa64514aeed6e34185d53559fc952/src/platformio/osww-server/src/main.cpp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
- Is your FE version `2.0.0`? See this line: https://github.com/mwood77/winderoo/blob/216bb8400f6aa64514aeed6e34185d53559fc952/src/angular/osww-frontend/package.json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

--

- Are you changing the motor direction through Home Assistant, or through the webapp?
    - The Home Assistant state will ("should") automatically update when Winderoo acknowledges the request. The webapp's state is only "fetched" on a refresh. For example, if you change the winding direction in HA, then you need to refresh the webapp (reload the page in the browser).

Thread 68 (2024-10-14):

Stepper motor support

mwood77, 2024-10-14:
### Discussed in https://github.com/mwood77/winderoo/discussions/61

<div type='discussions-op-text'>

<sup>Originally posted by **anjanbabu** August 12, 2024</sup>
This is an amazing project! love that it has a phone UI and OLED support!
I see a lot of DIY watch winders use small stepper motors like the [28BYJ-48 unipolar stepper motor with the ULN2003 motor driver](https://randomnerdtutorials.com/esp32-stepper-motor-28byj-48-uln2003/), it would be nice if you could enable the Winderoo code to work with these motors as well since they're so cheap and accessible. These fancy 3D printable gyro winders also use the same motors.
I did attempt to modify the code as [suggested](https://esp32.com/viewtopic.php?p=135879&sid=748c5ba2d0c311f7eed2870c0c47887c#p135879) by an ESP32 forum user, but I'm an ultra noob and I could not wrap my head around switching the PWM motor control code to a stepper motor one.</div>

tuliosilvajunior, 2025-01-07:
Hey, 1st of all thanks for your hard work.
I have the same situation here.
Do you have an idea when the Winderoo will be compatible with [28BYJ-48 unipolar stepper motor with the ULN2003 motor driver?
If you need any help testing software I would like to help.

KR,

Tulio

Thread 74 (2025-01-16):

multiple motors on ESP32

nogks, 2025-01-16:
### Discussed in https://github.com/mwood77/winderoo/discussions/73

<div type='discussions-op-text'>

<sup>Originally posted by **nogks** January 16, 2025</sup>
Hello,
thank you for the great work here.
I'm a beginner in this area. Is it possible to connect four motors
(Winderoo with OLED screen) to ESP32?
So two L298N.
Can the GPIO25 connection be connected to IN1 and IN3 and GPIO26 to IN2 and In4
(for two motors)?
Does the ESP32 have enough power to supply four motors?
Is it possible to expand the wiring diagram to four motors?
The motors should all run the same.

I hope you can help me</div>

mwood77, 2025-02-18:
Closing this issue and moving it to this discussion: https://github.com/mwood77/winderoo/discussions/73#discussioncomment-12234343

Closed 2025-02-18.

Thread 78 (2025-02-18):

Console showing 193391][E][vfs_api.cpp:105] open(): /littlefs/index.html does not exist, no permits for creation

tuliosilvajunior, 2025-02-18:
It's happening some random reboots, and in the console every page refresh the message below appears.

193391][E][vfs_api.cpp:105] open(): /littlefs/index.html does not exist, no permits for creation
[STATUS] - Motor turning clockwise
[STATUS] - Motor turning clockwise
[195080][E][vfs_api.cpp:105] open(): /littlefs/assets/i18n/en-US.json.gz does not exist, no permits for creation
[195190][E][vfs_api.cpp:105] open(): /littlefs/assets/i18n/pt-BR.json.gz does not exist, no permits for creation
[ERROR] - Failed to get time from Worldtime API

mwood77, 2025-02-19:
These messages are mostly OK - I'll breakdown what's happening though:

```
193391][E][vfs_api.cpp:105] open(): /littlefs/index.html does not exist, no permits for creation
     - this message is fine and can be ignored
```

```
[195080][E][vfs_api.cpp:105] open(): /littlefs/assets/i18n/en-US.json.gz does not exist, no permits for creation
[195190][E][vfs_api.cpp:105] open(): /littlefs/assets/i18n/pt-BR.json.gz does not exist, no permits for creation
     - this message states that it cannot find certain translations
```

```
[ERROR] - Failed to get time from Worldtime API
     - this is likely the problem. When this message shows up, it means the remote NTP server, "worldtime" has rate limited your winder; it isn't returning the time.
```

I'm in the process of adding some more customizations that allows you to manually set the winder's internal clock. You can see that here: https://github.com/mwood77/winderoo/pull/71

I hope to get this merged soon, and that should solve your timing issue...I hope.

tuliosilvajunior, 2025-02-21:
Is is possible to set a locally ntp server? Ex my home ntp server?
Any other clue for the LED? I'm trying to setup mine but is not working. When I plug the ground wire from the ESP32 to the OLED the ESP32 just freeze and reboot and stay freezed until I disconet the ground wire. If I use and external ground wire from an external power supply, it's not working too.

mwood77, 2025-02-24:
> Is is possible to set a locally ntp server? Ex my home ntp server?

That's an interesting idea actually 🤔 , unfortunately at this moment there isn't.

> Any other clue for the LED? I'm trying to setup mine but is not working. When I plug the ground wire from the ESP32 to the OLED the ESP32 just freeze and reboot and stay freezed until I disconet the ground wire. If I use and external ground wire from an external power supply, it's not working too.

Hmm, are you sure all of the pinouts are set correctly in the code?

Did you follow this wiring diagram?
- https://github.com/mwood77/winderoo/blob/main/docs/wiring-diagram.md#winderoo-with-oled-screen

Do you know if these parameters are correct for your OLED screen?
- https://github.com/mwood77/winderoo/blob/442278776d41fac8bb4505ff29be8cbfe71877bb/src/platformio/osww-server/src/main.cpp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
- https://github.com/mwood77/winderoo/blob/442278776d41fac8bb4505ff29be8cbfe71877bb/src/platformio/osww-server/src/main.cpp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
- https://github.com/mwood77/winderoo/blob/442278776d41fac8bb4505ff29be8cbfe71877bb/src/platformio/osww-server/src/main.cpp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

Specifically in the last point `0x3C` is an address. Are you sure that's compatible with yours too?

tuliosilvajunior, 2025-03-13:
Hey bro I just change some stuffs to use my personal ntp server or you can use the ntp.pool.org that is more reliable then the [world time.](http://worldtimeapi.org/api/ip)
On platform.io

lib_deps =
	esphome/AsyncTCP-esphome@^1.2.2
	esphome/ESPAsyncWebServer-esphome@^2.1.0
	Wire
	https://github.com/tzapu/WiFiManager.git
	https://github.com/bblanchon/ArduinoJson.git
	fbiego/ESP32Time@^2.0.0
	adafruit/Adafruit SSD1306@^2.5.9
	electromagus/ESPMX1508@^1.0.5
	dawidchyrzynski/home-assistant-integration@^2.1.0
        arduino-libraries/NTPClient@^3.2.1 //added this lib

on the main.cpp
I added
#include <NTPClient.h>
#include <WiFiUdp.h>

remove the:
String timeURL = "http://worldtimeapi.org/api/ip";

and change the to add the proper timezone

void setup() {
    WiFi.mode(WIFI_STA);
    Serial.begin(115200);
    setCpuFrequencyMhz(160);

    //(I live in Brazil so GMT -3)
    timeClient.setTimeOffset(-10800);  // GMT-3 offset in seconds (-3 * 60 * 60)

The GetTime fuction was changed and the last two lines (http.end(); and the extra closing brace) should be removed since we're using NTP now instead of HTTP.

void getTime() {
    timeClient.begin();
    timeClient.update();

    time_t epochTime = timeClient.getEpochTime();
    struct tm *ptm = gmtime ((time_t *)&epochTime);

    int currentYear = ptm->tm_year + 1900;
    int currentMonth = ptm->tm_mon + 1;
    int currentDay = ptm->tm_mday;
    int currentHour = timeClient.getHours();
    int currentMinute = timeClient.getMinutes();
    int currentSecond = timeClient.getSeconds();

    Serial.printf("[TIME] - Date: %d-%02d-%02d Time: %02d:%02d:%02d\n",
        currentYear, currentMonth, currentDay,
        currentHour, currentMinute, currentSecond);

    rtc.setTime(currentSecond, currentMinute, currentHour, currentDay, currentMonth, currentYear);

    timeClient.end();
}

mwood77, 2025-03-19:
@tuliosilvajunior #82 will introduce NTP based timekeeping. The current branch has a functional implementation if you care to try it out. Home Assistant integration will come soon.

mwood77, 2025-03-21:
@tuliosilvajunior NTP timekeeping has been merged into `main`.

Closed 2025-02-24.

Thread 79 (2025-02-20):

New install - getting a 404 resource not found when browsing to Winderoo on local network

loiphin, 2025-02-20:
Hi,

I did an install using the provided instructions to a ESP32 with VS Code and PlatformIO. That all appears to have gone well.

I can then browse to the Winderoo via its local Access Point. I then setup my local wireless network at home, and then reset the ESP32.

It comes up on my wifi network as I can ping it, but when trying to connect to http://winderoo.local, I get the following web page:

Winderoo

404 - Resource Not found

Any ideas what I can try to help debug this ?

loiphin, 2025-02-20:
Some more info from your monitor setup:

Hard resetting via RTS pin...
--- Terminal on COM8 | 115200 8-N-1
--- Available filters and text transformations: colorize, debug, default, direct, esp32_exception_decoder, hexlify, log2file, nocontrol, printable, send_on_enter, time
--- More details at https://bit.ly/pio-monitor-filters
--- Quit: Ctrl+C | Menu: Ctrl+T | Help: Ctrl+T followed by Ctrl+H
ets Jun  8 2016 00:22:57

rst:0x1 (POWERON_RESET),boot:0x13 (SPI_FAST_FLASH_BOOT)
configsip: 0, SPIWP:0xee
clk_drv:0x00,q_drv:0x00,d_drv:0x00,cs0_drv:0x00,hd_drv:0x00,wp_drv:0x00
mode:DIO, clock div:2
load:0x3fff0030,len:1184
load:0x40078000,len:13104
load:0x40080400,len:3036
entry 0x400805e4
*wm:AutoConnect
*wm:Connecting to SAVED AP: fish***
*wm:connectTimeout not set, ESP waitForConnectResult...
*wm:AutoConnect: SUCCESS
*wm:STA IP Address: 172.16.3.175
[STATUS] - LittleFS mounted
[STATUS] - connected to saved network
[   807][E][vfs_api.cpp:105] open(): /littlefs/settings.json does not exist, no permits for creation
[STATUS] - Failed to open configuration file, returning empty result
[STATUS] - mDNS started
[ERROR] - Failed to get time from Worldtime API
[ 36573][E][vfs_api.cpp:105] open(): /littlefs/index.html does not exist, no permits for creation <---- I BROWSE TO THE WINDERO HERE
[ 36575][E][vfs_api.cpp:105] open(): /littlefs/index.html.gz does not exist, no permits for creation
[ 36764][E][vfs_api.cpp:105] open(): /littlefs/favicon.ico does not exist, no permits for creation
[ 36766][E][vfs_api.cpp:105] open(): /littlefs/favicon.ico.gz does not exist, no permits for creation
[ 36772][E][vfs_api.cpp:105] open(): /littlefs/favicon.ico/index.html does not exist, no permits for creation
[ 36781][E][vfs_api.cpp:105] open(): /littlefs/favicon.ico/index.html.gz does not exist, no permits for creation

loiphin, 2025-02-20:
Some more testing using another board ...

Hard resetting via RTS pin...
--- Terminal on COM11 | 115200 8-N-1
--- Available filters and text transformations: colorize, debug, default, direct, esp32_exception_decoder, hexlify, log2file, nocontrol, printable, send_on_enter, time
--- More details at https://bit.ly/pio-monitor-filters
--- Quit: Ctrl+C | Menu: Ctrl+T | Help: Ctrl+T followed by Ctrl+H
e*wm:AutoConnect
*wm:No wifi saved, skipping
*wm:AutoConnect: FAILED for  13 ms
*wm:StartAP with SSID:  Winderoo Setup
*wm:AP IP address: 192.168.4.1
*wm:Starting Web Portal
[STATUS] - WiFi Config Portal running
[ 39654][E][WebServer.cpp:649] _handleRequest(): request handler not found
[ 40265][E][WebServer.cpp:649] _handleRequest(): request handler not found
[ 40348][E][WebServer.cpp:649] _handleRequest(): request handler not found
[ 43903][E][WebServer.cpp:649] _handleRequest(): request handler not found
[ 64691][E][WebServer.cpp:649] _handleRequest(): request handler not found
[ 68090][E][WebServer.cpp:649] _handleRequest(): request handler not found
[ 74418][E][WebServer.cpp:649] _handleRequest(): request handler not found
*wm:3 networks found
[ 84013][E][WebServer.cpp:649] _handleRequest(): request handler not found
*wm:Connecting to NEW AP: fishnet
*wm:connectTimeout not set, ESP waitForConnectResult...
*wm:Connect to new AP [SUCCESS]
*wm:Got IP Address:
*wm:172.16.3.185
[STATUS] - slow blink
ets Jun  8 2016 00:22:57

rst:0xc (SW_CPU_RESET),boot:0x17 (SPI_FAST_FLASH_BOOT)
configsip: 0, SPIWP:0xee
clk_drv:0x00,q_drv:0x00,d_drv:0x00,cs0_drv:0x00,hd_drv:0x00,wp_drv:0x00
mode:DIO, clock div:2
load:0x3fff0030,len:1184
load:0x40078000,len:13104
load:0x40080400,len:3036
entry 0x400805e4
*wm:AutoConnect
*wm:Connecting to SAVED AP: fis***
*wm:connectTimeout not set, ESP waitForConnectResult...
*wm:AutoConnect: SUCCESS
*wm:STA IP Address: 172.16.3.185
./components/esp_littlefs/src/littlefs/lfs.c:1229:error: Corrupted dir pair at {0x0, 0x1}
E (895) esp_littlefs: mount failed,  (-84)
E (897) esp_littlefs: Failed to initialize LittleFS
[STATUS] - LittleFS mounted
[STATUS] - connected to saved network
[  2336][E][vfs_api.cpp:105] open(): /littlefs/settings.json does not exist, no permits for creation
[STATUS] - Failed to open configuration file, returning empty result
[STATUS] - mDNS started
[ERROR] - Failed to get time from Worldtime API
[  9955][E][vfs_api.cpp:105] open(): /littlefs/index.html does not exist, no permits for creation
[  9957][E][vfs_api.cpp:105] open(): /littlefs/index.html.gz does not exist, no permits for creation

mwood77, 2025-02-20:
Looking at the logs, like here:

```
[ 9955][E][vfs_api.cpp:105] open(): /littlefs/index.html does not exist, no permits for creation
[ 9957][E][vfs_api.cpp:105] open(): /littlefs/index.html.gz does not exist, no permits for creation

and here

[ 36573][E][vfs_api.cpp:105] open(): /littlefs/index.html does not exist, no permits for creation <---- I BROWSE TO THE WINDERO HERE
[ 36575][E][vfs_api.cpp:105] open(): /littlefs/index.html.gz does not exist, no permits for creation
[ 36764][E][vfs_api.cpp:105] open(): /littlefs/favicon.ico does not exist, no permits for creation
[ 36766][E][vfs_api.cpp:105] open(): /littlefs/favicon.ico.gz does not exist, no permits for creation
[ 36772][E][vfs_api.cpp:105] open(): /littlefs/favicon.ico/index.html does not exist, no permits for creation
[ 36781][E][vfs_api.cpp:105] open(): /littlefs/favicon.ico/index.html.gz does not exist, no permits for creation
```

I'd wager a guess that you didn't flash the filesystem. You have to do that as well as "upload the code." Specifically step 7 here:
https://github.com/mwood77/winderoo/blob/main/docs/install-software.md#flashing-your-microcontroller

loiphin, 2025-02-20:
OMG.... thats embarrassing! Sorry to waste your time.

In your docs though, would you state what point 1. and point 2. mean in the diagram, so its clear for everyone?

Thanks again,

loiphin.

mwood77, 2025-02-20:
Sure, I can clarify that.

Do you mean, it would be better to illustrate the difference between steps 6 and 7 - which look very similar?

loiphin, 2025-02-20:
Yes please :) I think my brain thought okay, i have done everything , uploaded the firmware, and it should work. And stop reading properly :/....  I guess it wasnt clear there are two partitions, code and data.

loiphin, 2025-02-20:
Also , I am getting about 9RPM as speed, with no PWM. Do you work out the "turns per day" based on time, and an estimate of RPM ? Whats the RPM you worked out.

mwood77, 2025-02-20:
> Yes please :) I think my brain thought okay, i have done everything , uploaded the firmware, and it should work (and then I stop reading properly :/) .... I guess it wasnt clear there are two partitions, code and data.

👍  I'll squeeze this into an existing PR.

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

If you're willing to beta test, you can pull the code off this branch:
- https://github.com/mwood77/winderoo/pull/71

That branch contains configurable:
- clock (the current NTP server 429's Winderoo pretty badly)
- winding per-cycle time
- winding per-cycle pause time
- motor rotation timing

loiphin, 2025-02-20:
Awesome, just tried it now and it seems to work well :) Only difference I have found is that clockwise /counter clockwise is reversed in this build. No biggy, I can reverse the wiring to accomodate.

Thank you ever so much for building this project :) I have loved every minute of building it. It scratches so many itches of mine, mechanics, electronics, horologyl, 3d printing, and coding :)

mwood77, 2025-02-20:
Great, glad you've enjoyed it!

Please @me if you find any bugs in the code from that branch. Part of it was a significant rewrite, so I'm somewhat apprehensive to merge it.

Closed 2025-03-19.

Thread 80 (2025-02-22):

ESP32 Rebooting when disabling the OLED Screen - SSD1306 OLED

tuliosilvajunior, 2025-02-22:
I'm facing an issue when I connect the SSD1306 OLED nothing appears and if I try to disable using the GUI the ESP32 simply reboots.
Sometimes it froozen during the boot and to force the start I need to decouple the cabes from the ESP and then the boot sequence happens normally.
I tested with 2 different OLED, and they are working.

E (149552) task_wdt: Task watchdog got triggered. The following tasks did not reset the watchdog in time:
E (149552) task_wdt:  - async_tcp (CPU 0/1)
E (149552) task_wdt: Tasks currently running:
E (149552) task_wdt: CPU 0: IDLE
E (149552) task_wdt: CPU 1: IDLE
E (149552) task_wdt: Aborting.

abort() was called at PC 0x4010083c on core 0

Backtrace: 0x40083ccd:0x3ffbeccc |<-CORRUPTED

ELF file SHA256: 4d44ce74793736e9

Rebooting...
ets Jul 29 2019 12:21:46

rst:0xc (SW_CPU_RESET),boot:0x13 (SPI_FAST_FLASH_BOOT)
configsip: 0, SPIWP:0xee
clk_drv:0x00,q_drv:0x00,d_drv:0x00,cs0_drv:0x00,hd_drv:0x00,wp_drv:0x00
mode:DIO, clock div:2
load:0x3fff0030,len:1184
load:0x40078000,len:13104
load:0x40080400,len:3036
entry 0x400805e4
*wm:AutoConnect
*wm:Connecting to SAVED AP: myiot
*wm:connectTimeout not set, ESP waitForConnectResult...
*wm:AutoConnect: SUCCESS
*wm:STA IP Address: 192.168.1.197
[STATUS] - LittleFS mounted
[STATUS] - connected to saved network
[STATUS] - mDNS started
[STATUS] - HA Configured - Will attempt to connect to MQTT broker

mwood77, 2025-02-24:
I realized I posted my reply in the other issue, so here's a cross-post:

<hr>

> Any other clue for the LED? I'm trying to setup mine but is not working. When I plug the ground wire from the ESP32 to the OLED the ESP32 just freeze and reboot and stay freezed until I disconet the ground wire. If I use and external ground wire from an external power supply, it's not working too.

Hmm, are you sure all of the pinouts are set correctly in the code?

Did you follow this wiring diagram?
- https://github.com/mwood77/winderoo/blob/main/docs/wiring-diagram.md#winderoo-with-oled-screen

Do you know if these parameters are correct for your OLED screen?
- https://github.com/mwood77/winderoo/blob/442278776d41fac8bb4505ff29be8cbfe71877bb/src/platformio/osww-server/src/main.cpp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
- https://github.com/mwood77/winderoo/blob/442278776d41fac8bb4505ff29be8cbfe71877bb/src/platformio/osww-server/src/main.cpp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
- https://github.com/mwood77/winderoo/blob/442278776d41fac8bb4505ff29be8cbfe71877bb/src/platformio/osww-server/src/main.cpp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

Specifically in the last point `0x3C` is an address. Are you sure that's compatible with yours too?

tuliosilvajunior, 2025-02-24:
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

Hey I checked everything replaced all cables and the power supply. Everything now is working like a charm. Thank you again about your hard work.
Any plan to incorporate multiples winderoo units to be managed together?

mwood77, 2025-02-24:
I hit a snag getting multiple units networked together. I plan to look at it again when I have time to do a significant refactor . SO it's in the works, sometime soon ™  😉

Closed 2025-02-24.

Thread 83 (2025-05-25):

Trouble merging with Osww and winderoo

joegonow, 2025-05-25:
this is very humbling for I'm very new. I enjoy your work and I'm stuck. I can get osww working with esp32 board but when it comes to in integration with winderoo I'm stuck. I apologize of the inconvenience can you please tell me how to integrate the two ? remember I'm very new at this and this is my first project.

mwood77, 2025-05-25:
So navigating to `winderoo.local` in your web browser brings up the UI on your phone/tablet/computer?

joegonow, 2025-05-25:
Yes that is correct. I can get into the interface but  my motor does not spin.  My understanding is your program is an add on to osww. When I clear my esp32 and load osww on the motor spins. As soon as I add your code during the upload process the motor stops. I set up the WiFi and go to the winderloo.local and try to activate the motor I can’t get it to work.

Get Outlook for iOS<https://aka.ms/o0ukef>
________________________________
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

joegonow, 2025-05-25:
[image: {154920A8-9558-453A-9BD6-DAA02347C065}.png]

When following your steps I see motor turning but my motor is not spinning

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

mwood77, 2025-05-25:
Wonderful - glad you got it working! No problem, and enjoy your build!

joegonow, 2025-05-26:
Do you know what would cause the screen to look like this ?

Get Outlook for iOS<https://aka.ms/o0ukef>
________________________________
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

joegonow, 2025-05-26:
Let’s try this.  The screen is all white with black dots. With the exception of the top

Get Outlook for iOS<https://aka.ms/o0ukef>
________________________________
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

mwood77, 2025-05-27:
conversation moved to #84

Closed 2025-05-27.

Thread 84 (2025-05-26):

SSD 1306 looks all snowy

joegonow, 2025-05-26:
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

I have tried two different oleds and get the same result. I have shortened the wires and even upgraded wires with solder below is the exact description of the oleds

MakerFocus 2pcs 1.3 Inch I2C IIC OLED Display Module 128 x 64 Pixel SSD1306 Self-Luminous Display Board for Arduino/Raspberry Pi/ESP32

mwood77, 2025-05-27:
Ah I see!

OK, that can mean a few things. Sounds like you've checked your wiring connections already, which is good.

SO the next thing to check; did you tell Winderoo to compile with OLED support? That's included in Step 3, [**Build Options - (PWM, OLED, Home Assistant)**](https://github.com/mwood77/winderoo/blob/main/docs/install-software.md#flashing-your-microcontroller).

If not, it's pretty simple. All you need to do is open up Visual Studio Code and find a file called `platform.io`. In that file you'll see a block of text labeled `build_flags`. See here: https://github.com/mwood77/winderoo/blob/216bb8400f6aa64514aeed6e34185d53559fc952/platformio.ini#L23-L26

By default, OLED screens are disabled - they're an optional build item.

To enable your OLED, you must change the flag `-D OLED_ENABLED=false` to `-D OLED_ENABLED=true`. Then skip to step 5 and Step 6; this will re-compile the firmware and flash it to your ESP32. If everything went well, your screen should be working.

---

If the screen still doesn't work, this means you may need to make some changes to the code elsewhere. We can tackle that after you've double checked your ESP32's pinout, the wiring, and re-flashed with the OLED enabled flag.

joegonow, 2025-05-27:
I decided to buy a different brand of screen. It was dropped off today and I enabled the Olde from your steps above and it works beautifully. After further review the first Oled is a SSD1306 BUT it runs off a SSD106 chipset. The new Oled is SSD1306 and runs off SSD1306 chipset. Thank you for all your help

Closed 2025-05-27.

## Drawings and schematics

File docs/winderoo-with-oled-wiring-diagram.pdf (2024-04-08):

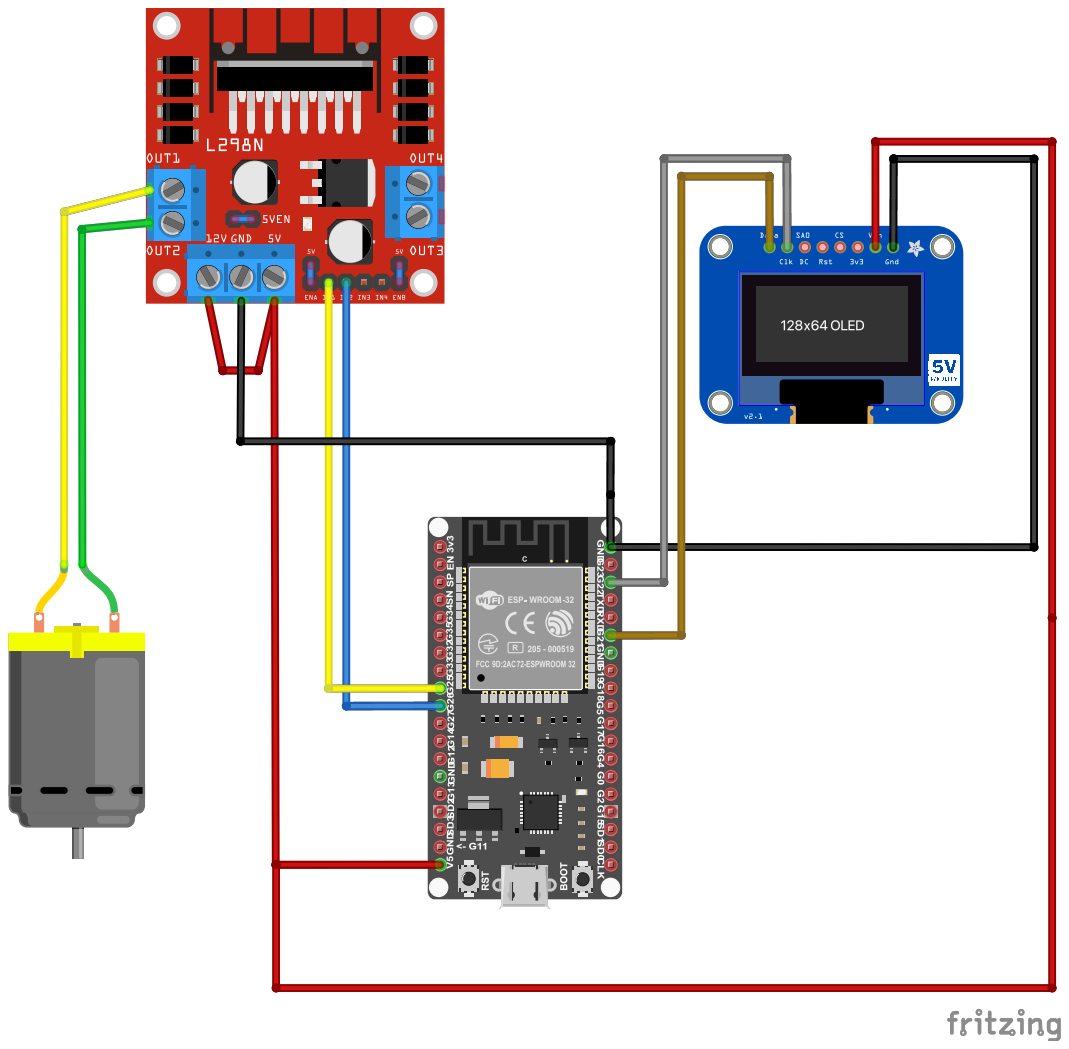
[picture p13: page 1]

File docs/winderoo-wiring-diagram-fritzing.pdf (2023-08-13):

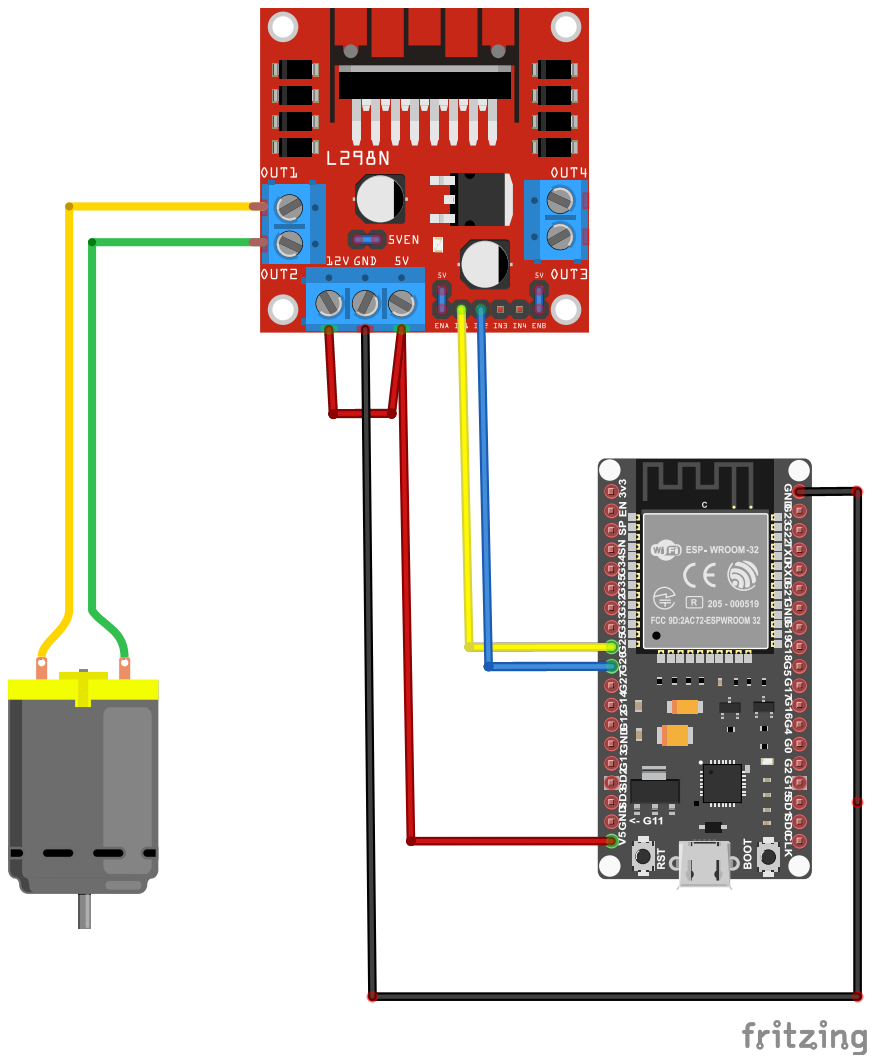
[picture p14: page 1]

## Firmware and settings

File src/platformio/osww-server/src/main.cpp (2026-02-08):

#include <Arduino.h>
#include <WiFiManager.h>
#include <LittleFS.h>
#include <ArduinoJson.h>
#include <HTTPClient.h>
#include <ESPmDNS.h>
#include <ESP32Time.h>
#include <NTPClient.h>
#include <WiFiUdp.h>

#ifdef OLED_ENABLED
	#include <SPI.h>
	#include <Wire.h>
	#include <Adafruit_GFX.h>
	#include <Adafruit_SSD1306.h>
#endif

#include "./utils/LedControl.h"
#include "./utils/MotorControl.h"

#include "FS.h"
#include "ESPAsyncWebServer.h"

/*
 * *************************************************************************************
 * ********************************* CONFIGURABLES *************************************
 * *************************************************************************************
 *
 * If you purchased the motor listed in the guide / Bill Of Materials, these default values are correct!
 *
 * durationInSecondsToCompleteOneRevolution = how long it takes the watch to complete one rotation on the winder.
 * directionalPinA = this is the pin that's wired to IN1 on your L298N circuit board
 * directionalPinB = this is the pin that's wired to IN2 on your L298N circuit board
 * ledPin = by default this is set to the ESP32's onboard LED. If you've wired an external LED, change this value to the GPIO pin the LED is wired to.
 * externalButton = OPTIONAL - If you want to use an external ON/OFF button, connect it to this pin 13. If you need to use another pin, change the value here.
 *
 * If you're using a NeoPixel equipped board, you'll need to change directionalPinA, directionalPinB and ledPin (pin 18 on most, I think) to appropriate GPIOs.
 * Failure to set these pins on NeoPixel boards will result in kernel panics.
 */
// int durationInSecondsToCompleteOneRevolution = 8;
int directionalPinA = 25;
int directionalPinB = 26;
int ledPin = 0;
int externalButton = 13;

// OLED CONFIG
bool OLED_INVERT_SCREEN = false;
bool OLED_ROTATE_SCREEN_180 = false;
int SCREEN_WIDTH = 128; // OLED display width, in pixels
int SCREEN_HEIGHT = 64; // OLED display height, in pixels
int OLED_RESET = -1; // Reset pin number (or -1 if sharing Arduino reset pin)

// Home Assistant Configuration
const char* HOME_ASSISTANT_BROKER_IP = "YOUR_HOME_ASSISTANT_IP";
const char* HOME_ASSISTANT_USERNAME = "YOUR_HOME_ASSISTANT_LOGIN_USERNAME";
const char* HOME_ASSISTANT_PASSWORD = "YOUR_HOME_ASSISTANT_LOGIN_PASSWORD";
/*
 * *************************************************************************************
 * ******************************* END CONFIGURABLES ***********************************
 * *************************************************************************************
 */

/*
 * DO NOT CHANGE THESE VARIABLES!
 */
String timeURL = "http://worldtimeapi.org/api/ip";
String settingsFile = "/settings.json";
unsigned long rtc_epoch;
unsigned long estimatedRoutineFinishEpoch;
unsigned long previousEpoch;
unsigned long startTimeEpoch;
bool reset = false;
bool routineRunning = false;
bool configPortalRunning = false;
bool screenSleep = false;
bool screenEquipped = OLED_ENABLED;
struct RUNTIME_VARS
{
	String status = "";
	String rotationsPerDay = "";
	String direction = "";
	String hour = "00";
	String minutes = "00";
	String winderEnabled = "1";
	String timerEnabled = "0";
	String customWindDuration = "";
	String customWindPauseDuration = "";
	int customDurationInSecondsToCompleteOneRevolution = 8;
	float gmtOffset = 0.0;
	bool dst = false;
	bool screenScheduleEnabled = false;
	String screenScheduleStartTime = "00:00";
	String screenScheduleEndTime = "00:00";
	bool screenSleep = false;
	float cycleProgress = 0.0; // 0.0 to 1.0
};

const float utcOffsetValues[] = {
	-12, -11, -10, -9.5, -9, -8, -7, -6, -5, -4.5, -4, -3.5, -3, -2, -1, 0,
	1, 2, 3, 3.5, 4, 4.5, 5, 5.5, 5.75, 6, 6.5, 7, 8, 8.75, 9, 9.5, 10, 10.5,
	11, 11.5, 12, 12.75, 13, 14
};

/*
 * DO NOT CHANGE THESE VARIABLES!
 */
RUNTIME_VARS userDefinedSettings;
LedControl LED(ledPin);
WiFiManager wm;
AsyncWebServer server(80);
HTTPClient http;
WiFiClient client;
ESP32Time rtc;
String winderooVersion = "4.0.1";
WiFiUDP ntpUDP;
NTPClient timeClient(ntpUDP);

#if PWM_MOTOR_CONTROL
	MotorControl motor(directionalPinA, directionalPinB, true);
#else
	MotorControl motor(directionalPinA, directionalPinB);
#endif

#ifdef OLED_ENABLED
	Adafruit_SSD1306 display(SCREEN_WIDTH, SCREEN_HEIGHT, &Wire, OLED_RESET);
#endif

#ifdef HOME_ASSISTANT_ENABLED
	#include <ArduinoHA.h>

	HADevice device;
	HAMqtt mqtt(client, device);

	// Define HA Sensors
	HASwitch ha_oledSwitch("oled");
	HANumber ha_rpd("rpd");
	HASelect ha_selectDirection("direction");
	HASwitch ha_timerSwitch("timerEnabled");
	HAButton ha_startButton("startButton");
	HAButton ha_stopButton("stopButton");
	HASelect ha_selectHours("hour");
	HASelect ha_selectMinutes("minutes");
	HASwitch ha_powerSwitch("power");
	HASensor ha_rssiReception("rssiReception");
	HASensor ha_activityState("activity");

	// Define HA Sensors (Setting & Customization)
	HANumber ha_customWindDuration("customWindDuration");
	HANumber ha_customWindPauseDuration("customWindPauseDuration");
	HASensor ha_currentEpoch("currentEpoch");
	HANumber ha_customDurationInSecondsToCompleteOneRevolution("customDurationInSecondsToCompleteOneRevolution");
	HASelect ha_rtcGmtOffset("rtcGmtOffset");
	HASwitch ha_rtcDST("rtcDST");
	
	// Define HA Sensors for Screen Scheduling
	HASwitch ha_screenScheduleEnabled("screenScheduleEnabled");
	HASelect ha_screenScheduleStartHour("screenScheduleStartHour");
	HASelect ha_screenScheduleStartMinute("screenScheduleStartMinute");
	HASelect ha_screenScheduleEndHour("screenScheduleEndHour");
	HASelect ha_screenScheduleEndMinute("screenScheduleEndMinute");
#endif

void drawCentreStringToMemory(const char *buf, int x, int y)
{
    int16_t x1, y1;
    uint16_t w, h;
    display.getTextBounds(buf, 0, y, &x1, &y1, &w, &h); //calc width of new string
    display.setCursor(x - (w / 2), y);
    display.print(buf);
}

void toggleDrawSavingIcon(bool showOnDisplay = false)
{
	if (showOnDisplay) 
	{
		// Write to screen buffer
		display.drawCircle(4, 4, 2, WHITE);
		return;
	}
	
	// remove icon from screen buffer
	display.drawCircle(4, 4, 2, BLACK);
	return;
}

static void drawStaticGUI(bool drawHeaderTitle = false, String title = "Winderoo") {
	if (OLED_ENABLED)
	{
		display.clearDisplay();

		display.setTextSize(1);
		display.setTextColor(WHITE);

		if (drawHeaderTitle)
		{
			drawCentreStringToMemory(title.c_str(), 64, 3);
		}
		// top horizontal line
		display.drawLine(0, 14, display.width(), 14, WHITE);
		// vertical line
		display.drawLine(64, 14, 64, 50, WHITE);
		// bottom horizontal line
		display.drawLine(0, 50, display.width(), 50, WHITE);

		display.setCursor(4, 18);
		display.println(F("TPD"));

		display.setCursor(71, 18);
		display.println(F("DIR"));

		display.display();
	}
}

static void drawTimerStatus() {
	if (OLED_ENABLED)
	{
		if (userDefinedSettings.timerEnabled == "1")
		{
			// right aligned timer
			display.fillRect(60, 54, 64, 13, BLACK);
			display.setCursor(60, 56);
			display.print("TIMER " + userDefinedSettings.hour + ":" + userDefinedSettings.minutes);
		}
		else
		{
			display.fillRect(60, 54, 68, 13, BLACK);
		}
	}
}

static void drawWifiStatus() {
	if (OLED_ENABLED)
	{
		// left aligned cell reception icon
		display.drawTriangle(4, 54, 10, 54, 7, 58, WHITE);
		display.drawLine(7, 58, 7, 62, WHITE);

		// Clear reception bars
		display.fillRect(12, 54, 58, 10, BLACK);

		if (WiFi.RSSI() > -50)
		{
			// Excellent reception - 4 bars
			display.fillRect(14, 55+8, 2, 2, WHITE);
			display.fillRect(18, 55+6, 2, 4, WHITE);
			display.fillRect(22, 55+4, 2, 6, WHITE);
			display.fillRect(26, 55+2, 2, 8, WHITE);
			if (HOME_ASSISTANT_ENABLED)	ha_rssiReception.setValue("Excellent");
		}
		else if (WiFi.RSSI() > -60)
		{
			// Good reception - 3 bars
			display.fillRect(14, 55+8, 2, 2, WHITE);
			display.fillRect(18, 55+6, 2, 4, WHITE);
			display.fillRect(22, 55+4, 2, 6, WHITE);
			if (HOME_ASSISTANT_ENABLED) ha_rssiReception.setValue("Good");
		}
		else if (WiFi.RSSI() > -70)
		{
			// Fair reception - 2 bars
			display.fillRect(14, 55+8, 2, 2, WHITE);
			display.fillRect(18, 55+6, 2, 4, WHITE);
			if (HOME_ASSISTANT_ENABLED) ha_rssiReception.setValue("Fair");
		}
		else
		{
			// Terrible reception - 1 bar
			display.fillRect(14, 55+8, 2, 2, WHITE);
			if (HOME_ASSISTANT_ENABLED) ha_rssiReception.setValue("Poor");
		}
	}
}

static void drawProgressBar(float progress) {
	if (OLED_ENABLED && !screenSleep)
	{
		// Clear the progress bar area
		display.fillRect(0, 50, display.width(), 2, BLACK);
		
		// Calculate progress bar width
		int progressWidth = (int)(progress * display.width());
		
		// Draw the progress bar
		display.fillRect(0, 50, progressWidth, 2, WHITE);
	}
}

static void drawDynamicGUI() {
	if (OLED_ENABLED && !screenSleep)
	{
		display.fillRect(8, 25, 54, 25, BLACK);
		display.setCursor(8, 30);
		display.setTextSize(2);
		display.print(userDefinedSettings.rotationsPerDay);

		display.fillRect(66, 25, 62, 25, BLACK);
		display.setCursor(74, 30);
		display.print(userDefinedSettings.direction);
		display.setTextSize(1);

		// Draw progress bar
		drawProgressBar(userDefinedSettings.cycleProgress);

		drawWifiStatus();
		drawTimerStatus();

		display.display();
	}
}

static void drawNotification(String message) {
	if (OLED_ENABLED && !screenSleep)
	{
		display.setCursor(0, 0);
		display.drawRect(0, 0, 128, 14, WHITE);
		display.fillRect(0, 0, 128, 14, WHITE);
		display.setTextColor(BLACK);
		drawCentreStringToMemory(message.c_str(), 64, 3);
		display.display();
		display.setTextColor(WHITE);
		delay(200);
		display.setCursor(0, 0);
		display.drawRect(0, 0, 128, 14, BLACK);
		display.fillRect(0, 0, 128, 14, BLACK);
		display.setTextColor(WHITE);
		drawCentreStringToMemory(message.c_str(), 64, 3);

		// Underline notification, which is shared with Static GUI
		display.drawLine(0, 14, display.width(), 14, WHITE);
		display.display();
	}
}

template <int N> static void drawMultiLineText(const String (&message)[N]) {
	if (OLED_ENABLED && !screenSleep)
	{
		int yInitial = 20;
		int yOffset = 16;

		display.fillRect(0, 18, 128, 64, BLACK);

		for (int i = 0; i < N; i++)
		{
			if (i == 0)
			{
				drawCentreStringToMemory(message[i].c_str(), 64, yInitial);
			}
			else
			{
				drawCentreStringToMemory(message[i].c_str(), 64, yInitial + (yOffset * i));
			}
		}
	display.display();
	}
}

void pauseWindingAndNotify() {
	int pauseDuration = userDefinedSettings.customWindPauseDuration.toInt();
	for (int i = 0; i < pauseDuration; i++) {
		Serial.print("[STATUS] - Remaining seconds: ");
		Serial.println(pauseDuration - i);

		// Delay for 1000ms (1 second)
		delay(1000);
	}
}

// Home Assistant Helper Functions
/**
 * @brief Checks if Home Assistant configuration values are set.
 */
void checkHomeAssistantConfigValues() {
    if (strcmp(HOME_ASSISTANT_BROKER_IP, "YOUR_HOME_ASSISTANT_IP") == 0) {
        Serial.println("ERROR: HOME_ASSISTANT_BROKER_IP is not set! Please configure it in main.cpp");

		String brokerIpErrorMessage[3] = {"Boot Fail!", "HOME_ASSISTANT_BROKER_IP", "is not set!"};
		drawMultiLineText(brokerIpErrorMessage);

        while (1);  // Halt program execution
    }
    if (strcmp(HOME_ASSISTANT_USERNAME, "YOUR_HOME_ASSISTANT_LOGIN_USERNAME") == 0) {
        Serial.println("ERROR: HOME_ASSISTANT_USERNAME is not set! Please configure it in main.cpp");

		String usernameErrorMessage[3] = {"Boot Fail!", "HOME_ASSISTANT_USERNAME", "is not set!"};
		drawMultiLineText(usernameErrorMessage);

        while (1);  // Halt program execution
    }
    if (strcmp(HOME_ASSISTANT_PASSWORD, "YOUR_HOME_ASSISTANT_LOGIN_PASSWORD") == 0) {
        Serial.println("ERROR: HOME_ASSISTANT_PASSWORD is  not set! Please configure it in main.cpp");

		String passwordeErrorMessage[3] = {"Boot Fail!", "HOME_ASSISTANT_PASSWORD", "is not set!"};
		drawMultiLineText(passwordeErrorMessage);

        while (1);  // Halt program execution
    }
}

/**
 * @brief Returns the index corresponding to a given direction for Home Assistant.
 *
 * This function takes a direction string and returns an integer index that 
 * corresponds to the direction for Home Assistant. The mapping is as follows:
 * - "CCW" -> 0
 * - "BOTH" -> 1
 * - Any other string -> 2
 *
 * @param direction The direction string. Expected values are "CCW", "BOTH", or any other string.
 * @return int The index corresponding to the given direction.
 */
int getDirectionIndexForHomeAssistant(String direction)
{
	if (direction == "CCW")
	{
		return 0;
	}
	else if (direction == "BOTH")
	{
		return 1;
	}
	else
	{
		return 2;
	}
}

float mapRtcUtcOffsetForAPItoHomeAssistant(float currentOffset)
{
	for (int i = 0; i < 40; i++)
	{
		if (currentOffset == utcOffsetValues[i])
		{
			return i;
		}
	}

	return 0;
}

float mapRtcUtcOffsetSelectorForHomeAssistant(int index)
{
	Serial.print("[STATUS] - Mapping index ");
	Serial.print(index);
	Serial.print(" to GMT Offset: ");
	Serial.println(utcOffsetValues[index]);

	return utcOffsetValues[index];
}

/**
 * @brief Converts a given minute value to an index used by Home Assistant.
 *
 * This function takes a minute value and returns a corresponding index
 * that is used by Home Assistant. The mapping is as follows:
 * - 0 minutes -> index 0
 * - 10 minutes -> index 1
 * - 20 minutes -> index 2
 * - 30 minutes -> index 3
 * - 40 minutes -> index 4
 * - 50 minutes -> index 5
 * 
 * If the minute value does not match any of the predefined cases, the function
 * returns 0 by default.
 *
 * @param minuteValue The minute value to be converted to an index.
 * @return The index corresponding to the given minute value.
 */
int getTimerMinutesIndexForHomeAssistant(int minuteValue)
{
	switch(minuteValue)
	{
		case 0:
			return 0;
		case 10:
			return 1;
		case 20:
			return 2;
		case 30:
			return 3;
		case 40:
			return 4;
		case 50:
			return 5;
		default:
			return 0;
	}
}

/**
 * Calculates the duration and estimated finish time of the winding routine
 *
 * @return epoch - estimated epoch when winding routine will finish
 */
unsigned long calculateWindingTime()
{
	int tpd = atoi(userDefinedSettings.rotationsPerDay.c_str());

	long totalSecondsSpentTurning = tpd * userDefinedSettings.customDurationInSecondsToCompleteOneRevolution;

	// We want to rest every userDefinedSettings.customWindDuration (180 is default) minutes for userDefinedSettings.customWindPauseDuration (5 is default) seconds
	long totalNumberOfRestingPeriods = totalSecondsSpentTurning / userDefinedSettings.customWindDuration.toInt();
	long totalRestDuration = totalNumberOfRestingPeriods * userDefinedSettings.customWindPauseDuration.toInt();
	long finalRoutineDuration = totalRestDuration + totalSecondsSpentTurning;

	Serial.print("[STATUS] - Total winding duration: ");
	Serial.println(finalRoutineDuration);

	unsigned long epoch = rtc.getEpoch();
	unsigned long estimatedFinishTime = epoch + finalRoutineDuration;

	return estimatedFinishTime;
}
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
void loop()
{
	if (configPortalRunning)
	{
		wm.process();
		return;
	}

	if (reset)
	{
		if (OLED_ENABLED)
		{
			display.clearDisplay();
			drawNotification("Resetting");

			String rebootingMessage[2] = {"Device is", "rebooting..."};
			drawMultiLineText(rebootingMessage);
		}
		// fast blink
		triggerLEDCondition(2);

		Serial.println("[STATUS] - Stopping webserver");
		server.end();
		delay(600);
		Serial.println("[STATUS] - Stopping File System");
		LittleFS.end();
		delay(200);
		Serial.println("[STATUS] - Resetting Wifi Manager settings");
		wm.resetSettings();
		delay(200);
		Serial.println("[STATUS] - Restart device...");
		ESP.restart();
		delay(2000);
	}

	if (userDefinedSettings.timerEnabled == "1")
	{
		if (rtc.getHour(true) == userDefinedSettings.hour.toInt() &&
			rtc.getMinute() == userDefinedSettings.minutes.toInt() &&
			!routineRunning &&
			userDefinedSettings.winderEnabled == "1")
		{
			beginWindingRoutine();
			drawNotification("Winding Started");
		}
	}

	if (routineRunning)
	{
		unsigned long currentTime = rtc.getEpoch();

		if (rtc.getEpoch() < estimatedRoutineFinishEpoch)
		{

			// turn motor in direction
			motor.determineMotorDirectionAndBegin();
			int r = rand() % 100;

			if (r <= 25)
			{
				if ((strcmp(userDefinedSettings.direction.c_str(), "BOTH") == 0) && (rtc.getEpoch() - previousEpoch) > userDefinedSettings.customWindDuration.toInt())
				{
					motor.stop();
					Serial.print("[STATUS] - Pause for duration: ");
					Serial.println(userDefinedSettings.customWindPauseDuration);

					drawNotification("Cycle Pause");
					pauseWindingAndNotify();

					previousEpoch = rtc.getEpoch();

					int currentDirection = motor.getMotorDirection();
					motor.setMotorDirection(!currentDirection);
					Serial.println("[STATUS] - Motor changing direction, mode: " + userDefinedSettings.direction);
					
					drawNotification("Winding");
					motor.determineMotorDirectionAndBegin();
				}

				if ((rtc.getEpoch() - previousEpoch) > userDefinedSettings.customWindDuration.toInt())
				{
					motor.stop();
					Serial.print("[STATUS] - Pause for duration: ");
					Serial.println(userDefinedSettings.customWindPauseDuration);
					
					drawNotification("Cycle Pause");
					pauseWindingAndNotify();
					drawNotification("Winding");
					
					previousEpoch = rtc.getEpoch();
				}
			}
		}
		else
		{
			// Routine has finished
			userDefinedSettings.status = "Stopped";
			routineRunning = false;
			motor.stop();
			if (OLED_ENABLED && !userDefinedSettings.screenSleep)
			{
				drawNotification("Winding Complete");
			}

			if (HOME_ASSISTANT_ENABLED) ha_activityState.setValue("Winding Complete");

			bool writeSuccess = writeConfigVarsToFile(settingsFile, userDefinedSettings);
			if ( !writeSuccess )
			{
				Serial.println("[ERROR] - Failed to write updated configuration to file");
			}
		}
	}

	// Update Home Assistant state
	if (HOME_ASSISTANT_ENABLED)
	{
		mqtt.loop();
		ha_rssiReception.setValue(String(WiFi.RSSI()).c_str());
		ha_currentEpoch.setValue(std::to_string(rtc.getEpoch()).c_str());
	}

	// OLED Screen Scheduling Logic
	if (userDefinedSettings.screenScheduleEnabled && OLED_ENABLED)
	{
		int currentHour = rtc.getHour(true);
		int currentMinute = rtc.getMinute();
		String currentTimeStr = String(currentHour < 10 ? "0" : "") + String(currentHour) + ":" + String(currentMinute < 10 ? "0" : "") + String(currentMinute);
		
		// Parse start and end times
		int startHour = userDefinedSettings.screenScheduleStartTime.substring(0, 2).toInt();
		int startMinute = userDefinedSettings.screenScheduleStartTime.substring(3, 5).toInt();
		int endHour = userDefinedSettings.screenScheduleEndTime.substring(0, 2).toInt();
		int endMinute = userDefinedSettings.screenScheduleEndTime.substring(3, 5).toInt();
		
		// Convert to minutes for easier comparison
		int currentTimeMinutes = currentHour * 60 + currentMinute;
		int startTimeMinutes = startHour * 60 + startMinute;
		int endTimeMinutes = endHour * 60 + endMinute;
		
		// Check if current time is within the scheduled range
		bool shouldShowScreen = false;
		
		if (startTimeMinutes <= endTimeMinutes) {
			// Same day schedule (e.g., 09:00 to 17:00)
			shouldShowScreen = (currentTimeMinutes >= startTimeMinutes && currentTimeMinutes <= endTimeMinutes);
		} else {
			// Overnight schedule (e.g., 22:00 to 06:00)
			shouldShowScreen = (currentTimeMinutes >= startTimeMinutes || currentTimeMinutes <= endTimeMinutes);
		}
		
		if (shouldShowScreen && userDefinedSettings.screenSleep) {
			// Turn screen on
			userDefinedSettings.screenSleep = false;
			display.clearDisplay();
			drawStaticGUI(true, userDefinedSettings.status);
			drawDynamicGUI();
		} else if (!shouldShowScreen && !userDefinedSettings.screenSleep) {
			// Turn screen off
			userDefinedSettings.screenSleep = true;
			display.clearDisplay();
			display.display();
		}
	}
	// When scheduling is disabled, do not override screenSleep; let API/UI/HA control it

	// Update cycle progress
	if (routineRunning) {
		unsigned long currentTime = rtc.getEpoch();
		unsigned long totalDuration = estimatedRoutineFinishEpoch - startTimeEpoch;
		unsigned long elapsedTime = currentTime - startTimeEpoch;
		
		if (totalDuration > 0) {
			userDefinedSettings.cycleProgress = (float)elapsedTime / (float)totalDuration;
			// Clamp progress between 0 and 1
			if (userDefinedSettings.cycleProgress > 1.0) {
				userDefinedSettings.cycleProgress = 1.0;
			} else if (userDefinedSettings.cycleProgress < 0.0) {
				userDefinedSettings.cycleProgress = 0.0;
			}
		}
	} else {
		userDefinedSettings.cycleProgress = 0.0;
	}

	// Update OLED display
	if (OLED_ENABLED && !userDefinedSettings.screenSleep)
	{
		drawDynamicGUI();
	}

	// Update cycle progress
	if (routineRunning) {
		unsigned long currentTime = rtc.getEpoch();
		unsigned long totalDuration = estimatedRoutineFinishEpoch - startTimeEpoch;
		unsigned long elapsedTime = currentTime - startTimeEpoch;
		
		if (totalDuration > 0) {
			userDefinedSettings.cycleProgress = (float)elapsedTime / (float)totalDuration;
			// Clamp progress between 0 and 1
			if (userDefinedSettings.cycleProgress > 1.0) {
				userDefinedSettings.cycleProgress = 1.0;
			} else if (userDefinedSettings.cycleProgress < 0.0) {
				userDefinedSettings.cycleProgress = 0.0;
			}
		}
	} else {
		userDefinedSettings.cycleProgress = 0.0;
	}

	wm.process();

	awaitWhileListening(1);
}

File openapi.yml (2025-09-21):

openapi: 3.1.0
info:
  title: Winderoo API
  version: 4.0.0
servers:
  - url: http://winderoo.local/api/
    description: local development and deployed devices
tags:
  - name: Status
    description: Retrieve the current state of Winderoo
  - name: Modify
    description: Modify the state of Winderoo
paths:
  /timer:
    post:
      tags:
        - Modify
      summary: Change the timer state of Winderoo
      parameters:
        - in: query
          name: timerEnabled
          schema:
            type: integer
          description: Whether Winderoo should enable alarm-start winding; number represents a boolean where 0 == off and 1 == on.
          example: 1
      responses:
        '204':
          description: Successful opeation
        '400':
          description: Missing required field in request body
          content:
            text/plain:
              schema:
                type: string
                examples: 
                  - "Missing required field: 'tpd'"
        '500':
          description: Something went wrong when writing to memory or during deserialization
          content:
            text/plain:
              schema:
                type: string
                examples:
                  - Failed to deserialize request body
  /update:
    post:
      tags:
        - Modify
      summary: Change the state of Winderoo
      requestBody:
        $ref: '#/components/requestBodies/UpdateBody'
      responses:
        '204':
          description: Successful opeation
        '400':
          description: Missing required field in request body
          content:
            text/plain:
              schema:
                type: string
                examples: 
                  - "Missing required field: 'tpd'"
        '500':
          description: Something went wrong when writing to memory or during deserialization
          content:
            text/plain:
              schema:
                type: string
                examples:
                  - Failed to deserialize request body
  /status:
    get:
      tags:
        - Status
      summary: Get the current status of Winderoo
      responses:
        '200':
          description: Service is alive with current winder state
          content:
            application/json:
              schema:
                $ref: '#/components/schemas/Status'
  /power:
    post:
      tags:
        - Modify
      summary: Toggle whether Winderoo is on or off (hard off state)
      requestBody:
        $ref: '#/components/requestBodies/PowerBody'
      responses:
        '204':
          description: State toggled succesfully
        '400':
          description: Missing required field in request body
          content:
            text/plain:
              schema:
                type: string
                examples: 
                  - "Missing required field: 'winderEnabled'"
        '500':
          description: Something went wrong when writing to memory or during deserialization
          content:
            text/plain:
              schema:
                type: string
                examples: 
                  - Failed to deserialize request body
  /reset:
    get:
      tags:
        - Modify
      summary: Resets Winderoo's network settings; re-initializes winderoo with setup access point
      responses:
        '200':
          description: State toggled succesfully
          content:
            application/json:
              schema:
                $ref: '#/components/schemas/Resetting'
components:
  requestBodies:
    UpdateBody:
      description: a JSON object containing winderoo information
      required: true
      content:
        application/json:
          schema:
            $ref: '#/components/schemas/Update'
          example:
            tpd: "330"
            hour: "14"
            minutes: "50"
            timerEnabled: "0"
            action: "START"
            rotationDirection: "BOTH"
            screenSleep: false
            screenScheduleEnabled: false
            screenScheduleStartTime: "09:00"
            screenScheduleEndTime: "22:00"
            customWindDuration: 180
            customWindPauseDuration: 15
            customDurationInSecondsToCompleteOneRevolution: 8
            gmtOffset: -3.5
            dst: false
    PowerBody:
      description: a JSON object containing winderoo power information
      required: true
      content:
        application/json:
          schema:
            $ref: '#/components/schemas/Power'
          example:
            winderEnabled: "1"
  schemas:
    Power:
      type: object
      propertries:
        winderEnabled:
          type: string
          description:
            Whether Winderoo should enable alarm-start winding; number represents a boolean where 0 == off and 1 == on.
          examples:
            - 0
            - 1
    Update:
      type: object
      propertries:
        tpd:
          type: string
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

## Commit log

2023-01-31 fixed webserver + initial UI
    [main.cpp]
2023-02-01 add wifi and battery level indicators
2023-02-05 fix wifi connection success callback- #1
    [main.cpp]
2023-02-05 added time differential + ui & basic motor direction determination logic
2023-02-12 debug code + add motor control
2023-02-12 power consumption #3
2023-02-12 rollback wifi low power mode
2023-02-13 added progress bar & fix TPD change mid-cycle
    [main.cpp]
2023-02-14 added UI power toggle
2023-02-16 moved led control to dedicated class + added "snooze" indicator
2023-02-16 moved motor control to separate class
2023-02-16 added button read in main loop
2023-02-16 edit readme & update BOM
2023-02-17 add new doc & printing images
2023-02-20 add on/off state for timer
2023-03-04 add multi-clip to print guide
2023-06-11 rework button listener
2023-08-13 add wiring diagram and cleanup docs (and 2 bugs)
2023-10-17 update broken link in bom
2024-02-11 Bump socket.io-parser from 4.2.2 to 4.2.4 in /src/angular/osww-frontend (#23)
    Bumps [socket.io-parser](https://github.com/socketio/socket.io-parser) from 4.2.2 to 4.2.4.
    - [Release notes](https://github.com/socketio/socket.io-parser/releases)
    - [Changelog](https://github.com/socketio/socket.io-parser/blob/main/CHANGELOG.md)
    - [Commits](https://github.com/socketio/socket.io-parser/compare/4.2.2...4.2.4)
    ---
    updated-dependencies:
    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
2024-02-12 Refactor JSON implementation & change local storage setup (#26)
    * refactor json implementation & change local storage to use json
    * Update LED control messages
    * Update configurable values in main.cpp
    * Add CI workflow for PlatformIO and remove unnecessary Firefox installation
2024-02-23 Update German translations, add translation of current state to settings page
2024-02-26 Refactor endpoints to support request bodies (#37)
    * update openapi to reflect inteded changes
    * update api to handle request body
    * add timer endpoint
    * update FE to new post request bodies
    * refactor timerEnabled handling in FE
    * tweak loading bar
    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
2024-03-05 Return current window location href as API url (#40)
    * Return current window location href as API url
    * Add build-arduino
2024-03-29 bug - save state when winding completed (#46)
    [main.cpp]
2024-04-02 Add support for Português (#44)
    * add support for Português
    * add portuguese translations
    * attach build
2024-04-08 Support for OLED Screens (#47)
    * hackish oled implementation
    * bug - save state when winding complet
    * basic GUI
    * tweaks
    * formatting
    * more formatting
    * update documenation
    * update images
    * fix centering on multi-line messages
    * modify `drawStaticGUI()` method
    * Added timer and wifi reception to oled
    * add `_screen` related variables for front end
    * add `_screen` related flags in front end
    * add translations
    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
    [winderoo-with-oled.fzz]
2024-05-17 [Experimental] pwm motor control (#54)
    * experimental - pwm motor control
    * fix callout block
    * install-software edits
    * change channels
    * update to 20 rpm & 145 resolution
    * Update `motorSpeed` to `145` in MotorControl
    * Update bom-requirements to include MX1508 callout
    * typo in bom-requirements
    * Update bom-requirements.md
    * add timing duration in troubleshooting
    * fix link
    [MotorControl.cpp, main.cpp]
2024-05-17 add pwm callout using MX1508 (#56)
2024-10-08 Add home assistant integration (#66)
    * add home assistant integration
    * add remaining HA entities
    * update documentation & fix typos
    * typos
    * add conditional checks for `HOME_ASSISTANT_ENABLED`
    * add correct version to mqtt
    * fix a few typos in `install-software.md`
    * Update install-software.md
    [main.cpp]
2025-03-19 Add ability for users to customize certain behaviour (#71)
    * add customization card with custom winding time and custom pause time
    * Compute new cycle duration on customization changes
    * update oas
    * add clock ui
    * save icon in backend
    * change worldtime failure to a warning
    * send `rtc_selectedHour` and `rtc_selectedMinutes` to BE
    * simply clock logic and add ability to manually set it
    * consistent casing
    * add `customWindDuration` and `customWindPauseDuration` to state and parse it in update endpoint. Also provide values in status call
    * refactor timing comparison
    * update internal `calculateWindingTime()` prediction
    * customizable timing complete through web UI
    * add HA cycle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
    [main.cpp, openapi.yml]
2025-03-21 Migrate to NTP based timekeeping (#82)
    * update oas with gmtOffset and dst fields
    * update `settings.json` with `gmtOffset` and `dst`
    * add `arduino-libraries/NTPClient@^3.2.1` to `platformio.ini`
    * basic functionality to initialize, set, and configure `gmtOffset`
    * add dst to `/status` and `/update`
    * fix deprecation warning
    * bump fe version
    * update FE to use GMT offset and DST toggle
    * build & package FE 2.0.0
    * build & package FE 2.0.0
    * update docs
    * home assistant DST and UTC Offset
    * typo in user-manual
    * add ha config checker
    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
    [main.cpp, openapi.yml]
2025-07-06 ⌛ Added OLED progress bar for cycle progress (#86)
    * Added OLED progress bar for cycle progress
    * Fix OLED screen initialization - Enable OLED_ENABLED and add Wire.begin()
    * Revert OLED_ENABLED to false in platformio.ini
    * Optimize OLED display rendering with unified clearing and progress bar integration
    - Add clearDisplayArea() helper function for efficient screen clearing
    - Replace multiple fillRect() calls with single clearDisplayArea() call in drawDynamicGUI()
    - Consolidate display.display() calls to reduce screen refresh overhead
    - Improve code organization with better comments and structure
    * Fix progress bar overlap issue and bump version to 4.0.1
    - Move timer status Y positio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
    [main.cpp]
2025-09-21 🔆 Implemented OLED screen scheduling (#87)
    * Implemented OLED screen scheduling
    * Fixed parameter naming convention in settings component: - Updated updateScreenScheduleEnabled to use parameter for consistency with other methods
    * Added OLED screen scheduling support to backend
    * feat: Add OLED screen scheduling functionality
    Add new feature to schedule OLED display on/off times for power management
    and user convenience.
    Backend Changes:
    - Added screenScheduleEnabled, screenScheduleStartTime, screenScheduleEndTim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
    [main.cpp, openapi.yml]
2025-09-21 rebuild FE and attach, and update instructions doc with images (#90)
